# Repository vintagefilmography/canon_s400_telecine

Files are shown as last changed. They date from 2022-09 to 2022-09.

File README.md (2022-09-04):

# canon_s400_telecine
  
This is one of the simplest telecine systems that is capable of creating a very good quality 8mm video.
The setup consists of a modified Canon S400 projector and the T3i Canon camera. The setup provides the 8mm film capture running at  up to 8 FPS and generates the video at 1280x972 resolution for the super 8 film. The R8 resoolution is lower but still good quality. It is to be noted that the Laowa macro lens is capable of higher resolution but it makes the setup much trickier.  More on that later in this doc.  
The purpose of this  readme is to provide the instructions to the user on how to modify the existing 8mm canon projector for the video capture directly into the camera.  
Similar to other projects of this type, this one also requires several modifications to the projector including the light change, and motor speed change. The diffecence is that the capture is run asynchronously i.e. the projector speed is not matched to the camera FPS but instead it runs at any speed within the 8FPS  ransge.
A simple posprocessing script takes care of multiple duplicate frames and black any frames. 



##   Shutter Wheel Mod
The projector has three shutter blades. For this type of transfer it is necessary to remove two of the blades by snipping them off with the sheers. The blade that blanks out the film transition is left in.  
  
## Gate Mask Removal
This step is not completely necessary but it does provide film overscan and makes the film holes visible which some people like. The mask is a part of the S8/R8 switching mechanism. It is recommended to remove the mechanism and then cutting the masks out or bending them repetetively until they snap off. Be careful here because the components are very fragile.  

## Motor  Speed  
The motor speed should be reduced for 8 FPS operation. The unmodified projector low speed setting is still larger than 8  FPS. The speed reduction is achieved by installing a power resistor in series with the rheostat (speed adjust potentiometer).
  
Two 1000 Ohm, 10W resistors are used in series with the motor rotor to get the speed reduction.   
The bypass switch, labelled as 4FPS, bypasses the power resistors and gives the original speed. Can be useful for rewinding.  
The resistors are mounted on a custom aluminum heatsik as shown in the picture. The heatsink is secured down with a 4mm screw mounted on the top of the unit.

## Fan
The fan can be removed. It was required originally to cool the light and is no longer needed for the led light. For long scans a new fan can be attached to the back cover louvres to keep the resistors cool.  

## Light
The following light is recommended.  
https://www.amazon.com/gp/product/B07YSF3X8K/  
The mounting bracket design is located in the mechanical folder above.

## Camera Slider Mounting  
The following camera sider is used:  
https://www.bhphotovideo.com/c/product/193311-REG/Velbon_SUPER_MAG_SLIDER_Super_Mag_Slider.html
Two spacers are to be mounted underneath the slider mounting board. 
The board dimensions and the spacer stl file can be found in the mechanical folder.  

## Macro Lens
There are many out there that will do the job.  
Venus Laowa is a pretty good pick. It has more than enough magnification and good image quality and it is reasonably priced.
https://www.venuslens.net/product/laowa-25mm-f-2-8-2-5-5x-ultra-macro-2/  

## Assembly
Print out all of the parts from the mechanical folder. 
Attach the two spacers from the mechanical folder on the camera base board towards the edges of the board.

Drill two holes on the slider base board as shown in the following image:  

Drill the clearance holdes for the mounting bolts. Use 3/8"-16 bolts.  
Mount the slider onto the slider board.
 
Mount the slider and the slider base onto the main board. Drill a hole through the main board, spacer and the slider board as shown:  

If you plan to use the rubber bumpers under the main board then it is not necessary to drill a clearance hole for the 
mounting screw head. But if no bumpers are used a shallow clearance hole has to be drilled so that the screw head 
is not protruding through the bottom of the main board which could scratch the surface of the table or whatever stand you are using for the 
scanner. Size 10 bolt is adequate. A wingnut is also handy when it comes time to dismentle the unit. Adjust the wingnut tension so that the slider and the camera 
sit solid on the main board. A small vertical adjustment can be made by instrting a thin plastic card under the second spacer.
Mount the macro lens onto the camera.  
Mount the camera onto the slider.  
Turn the camera on. Position the projector close to the camera so that the film gate is visible and adjust the zoom so that the film gate covers most of the camera display. Adjust focus by turning the slider focus knob.   

## Camera  Settings
Make sure the battery is fully charged and the SD card is empty. 
Turn the camera on and make sure the film is in focus. Try to adjust the projector so that the film is on the   
righ hand side in the oreview window or on the HDMI monitor window. With the Laowa lens teh alignment between the  
camera and the projector is  not dead on which could cause the depth of files issues. So, positioning the film image to the   
right will mitigate the issue. Will not be perfect but pretty close to it.  
Set the F stop on teh lens to 2.8. If you notice some brurriness at the edges then set it to 4.  
Set ISO to 800.  
Adjust the shutter (wheel at the front of the camera) so that the image is bright enough.  
Ususlly anywhere between 200 and 300 should be OK.
Set the camera in video mode and set to 1920x1080/30FPS

## Operation

Load the film.  
Connect the camera HDMI port to a monitor. 
Turn the LED light on.  
Turn the camera on and press the live view button. 
Press Live View again to start recording.  
Run the projector and set the speed to minimum by using the speed knob at the front.  
Make sure that the resistor bypass switch is off.  
Once done with the recording, stop the camera by pressing the live view.  
Turn the camera off.  
Turn the projector off.  
Remove the SD card and copy the video to a PC.

## Post Processing  the video to a PC.  
The video will contain many frames with dark bands which are result of asynchronous operation.  
In another words the camera and the projector are not synched and the camera will pick up frames that contsin film transitions.
Additionally, since the frame rate of the camera is much faster than the projectors, there will be lots of duplicate frames.
It is easy to remove the duplicates and the transition frames by using the Avisynth remove_dups script.  
The first step in getting the the script working is to get Avisynth from:
http://avisynth.nl/index.php/Main_Page
Avisynth does not run as a standalone application. It is a tool that allows video editors and viewers to run the script.  
The script is essentially a text file that contains the avisynth commands for video processing.  
One video  tool that is very handy for video processing is called VirtualDub. 
In addition to basic video processing, VirtialDub reads the avisynth script as well.  
Download VirtualDub from here:
https://sourceforge.net/projects/vdfiltermod/files/
Run VirtualDub.  
Should get a dub window that looks like the following picture:
  

Using the avisynth script can get a bit tricky because there are some many plugins out there and you will usually  
run into a plugin missing error. That is why I put a complete scripts zip file in in the software folder. This contains  
the required plugins.  
Download the zip file and unzip it somewhere in your work directory. 

Go to the scripts directory and open up remove_dups.avs in any text editor like Notepad or any other text editor..
Change the clip source path to wherever the clip is stored.
#=============================================================================================
# Clip source.
#=============================================================================================

film = "F:\canon\clip1_raw.avi"  # source clip, you must specify the full path here  
  
Change the threshold:  
source= AviSource(film).assumefps(play_speed).trim(trim_begin,0).converttoYV12()  
trimming= framecount(source)-trim_end  
source1= trim(source,0,trimming)  
source2= AssumeTFF(source1)  
fc=Framecount(source2)  
source3 = GetDups(source2,mode=-2,threshold=30.0)  
source4 = Trim(source3,0,fc/3).coloryuv(autowhite=true)  
#Eval(film)  
  
Here it is set to 30. Lower threshold will have less chance of saving the bad frames but if it is too low it may remove some good frames.  
It is a good idea to check the frame count uo front by running teh projector at low speed and counting the frames for a minute or two to  
determine the frame rate and then run the complete reel and multiply the rate with duration. Alternatively a rough frame count can be obtained from the 
size of the reel.

Once done with the script, just drag the script file into the VirtualDub window.
After a minute or so the video first frame will be displayed.  
At that point, set the video compression in the video pulldown and save the video.
No further processing will be required, although soemtimes you may get a few blank frames.
If that happens run the remove_black_frames.avs script included here.

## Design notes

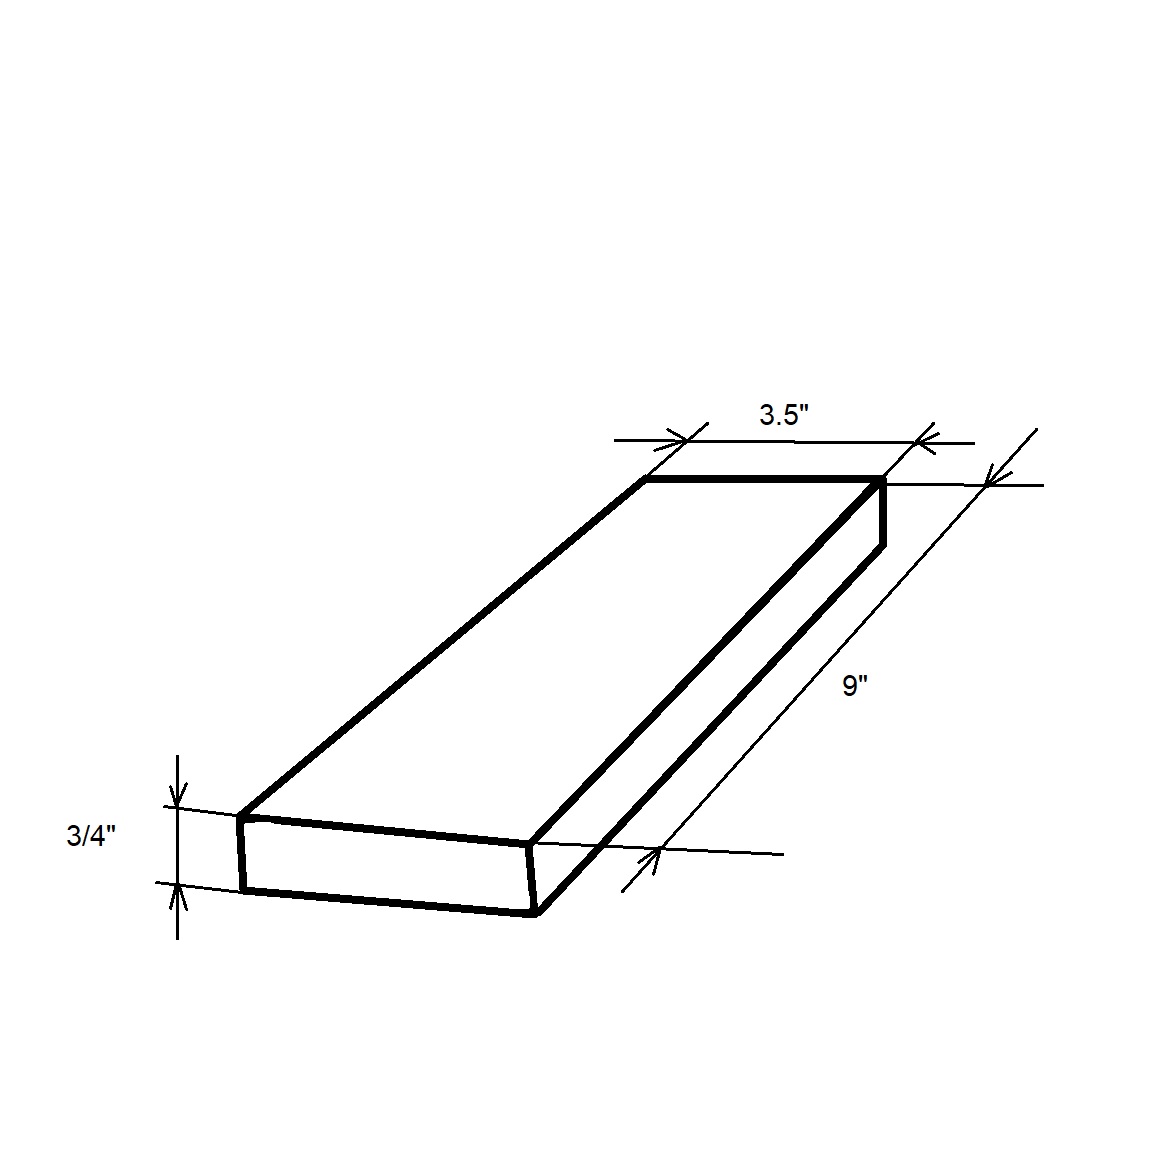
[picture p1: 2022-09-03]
mechanical/camera_base.jpg

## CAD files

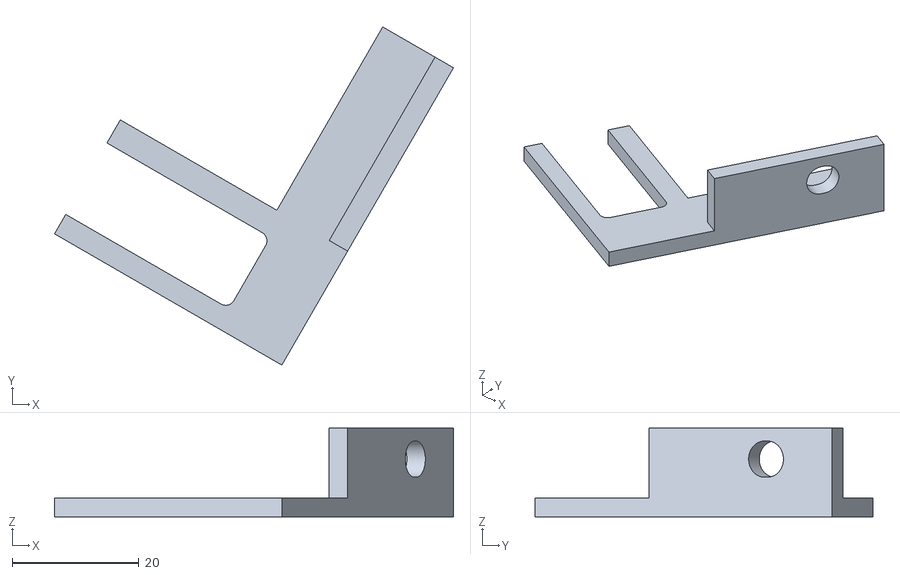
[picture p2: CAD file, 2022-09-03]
mechanical/lamp_adapter.stl
62.9 x 53.3 x 14.0

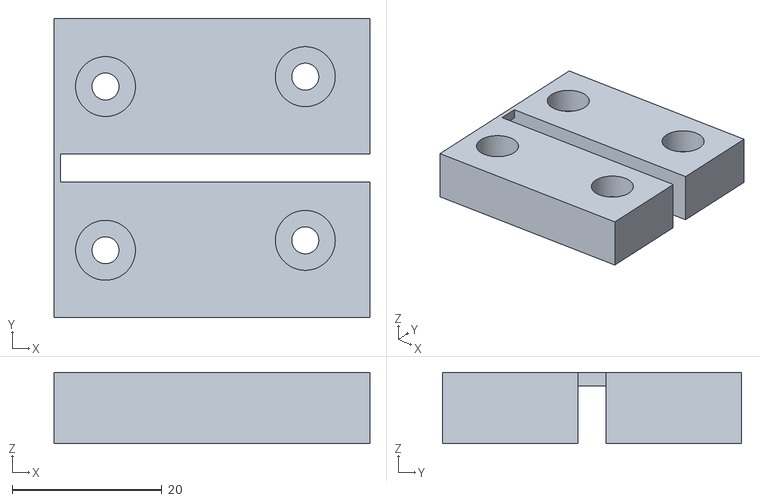
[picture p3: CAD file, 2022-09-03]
mechanical/spacer.stl
42.2 x 39.9 x 9.48
